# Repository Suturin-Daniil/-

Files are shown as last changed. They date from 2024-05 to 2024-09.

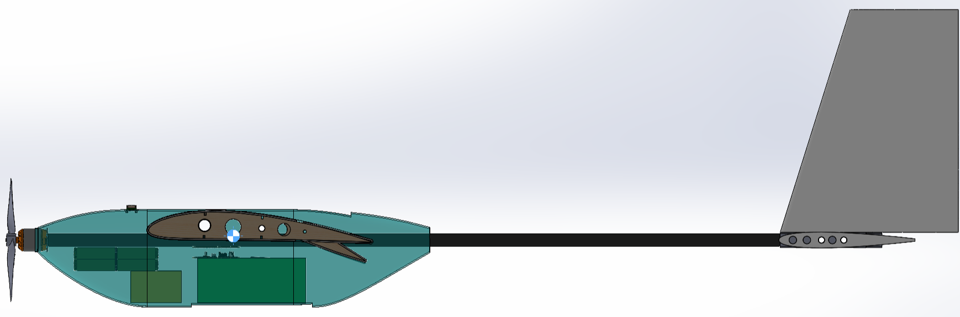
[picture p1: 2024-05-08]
PreliminaryDesign/Images/SideViewTransparentWithCG.png

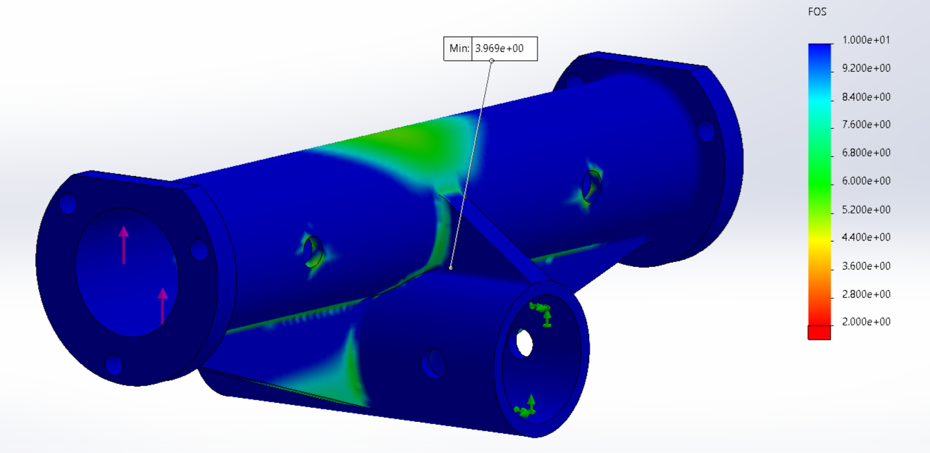
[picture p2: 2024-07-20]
Manufacturing/Отчет/ConnectorFOS.png

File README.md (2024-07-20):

# Репозиторий команды ФАКИшники СКАТ2024

В этом репозитории содержится процесс разработки ЛА командой "ФАКИшники" в рамках студенческого конкурса авиамодельного творчества СКАТ 2024.

## Структура репозитория

- **ConceptualDesign** - папка содержит резльтаты концептуального дизайна ЛА. Описание аэродинамической схемы. Начальная модель ЛА

- **PreliminaryDesign** - папка промежуточного отчета, содержащая детализированую модель ЛА, начальные аэродинамические и прочностные исследования. Описано бортовое оборудование

- **Manufacturing** - папка производственного отчета, содержит конечный вариант детальной модели ЛА, представлены результаты численного моделирования полета ЛА, статической и динамической стабильности. Прочностные расчеты

- **FlightController** - содержит электрические схемы полетного контроллера и платы распределения питания собственной разработки, а также проекты EasyEDA. Приложены gerber файлы печатых плат

- **Costings** - смета на полетный контроллер и ЛА

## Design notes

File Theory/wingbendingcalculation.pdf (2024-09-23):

### Wing Bending Calculations

Lab 10 Lecture Notes

Nomenclature

L

y | spanwise coordinate
q | net beam loading
S shear
M bending moment
θ | deflection angle (= dw/dx)
w | deflection
κ | local beam curvature
′ | lift/span distribution

′

S

η | normalized spanwise coordinate (= 2y/b)
c | local wing chord
wing | wing area
b | wing span
λ | taper ratio
E Young’s modulus
δ tip deflection
N load factor
m wing mass/span distribution I bending inertia
i | spanwise station index
n | last station index at tip

L lift
W weight
g | gravitational acceleration
()o | quantity at wing root

Loading and Deflection Relations
The net wing beam load distribution along the span is given by
′ | ′ q(y) = L (y) − N g m (y) | (1)

where m ′ (y) is the local mass/span of the wing, and N is the load factor. In steady level flight we have N = 1. The net loading q(y) produces shear S(y) and bending moment M(y) in the beam structure. This resultant distribution produces a deflection angle θ(y), and deflection w(y) of the beam, as sketched in Figure 1.

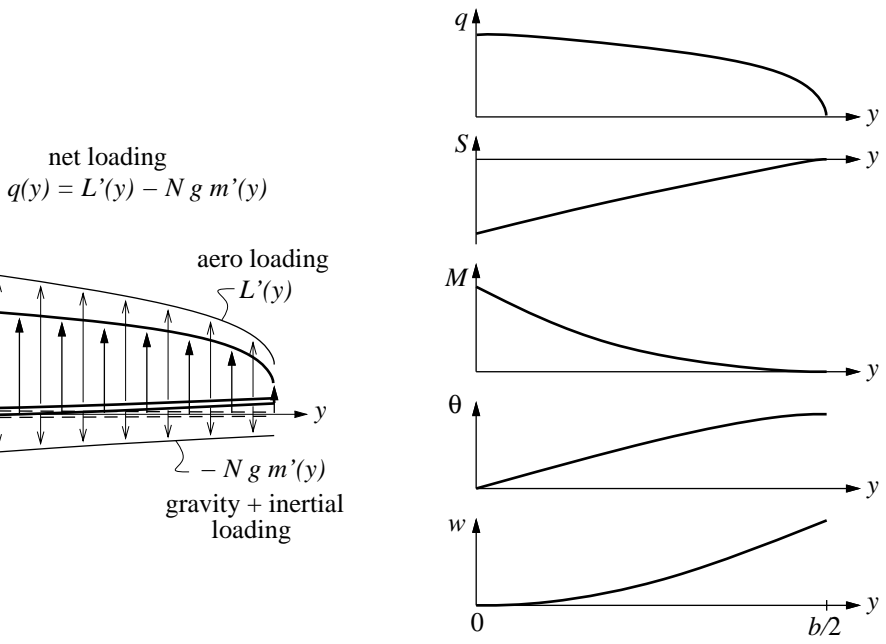
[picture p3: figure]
net loading q(y) = L’(y) − N g m’(y); aero loading; gravity + inertial; loading
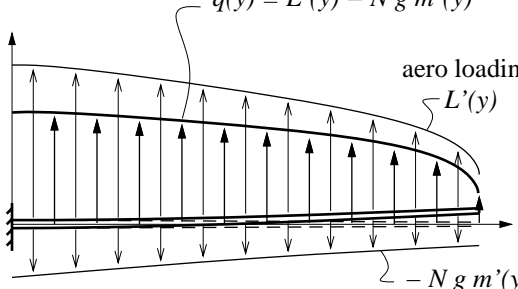
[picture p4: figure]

Figure 1: Aerodynamic and mass loadings, and resulting structural loads and deflection.

The standard differential equations derived via simple Bernoulli-Euler beam model, with the primary structural axis along the y direction, relate the loads and deflections to the loading q(y) and the bending stiffness EI(y).
dS | = q dy | (2)
dM = S dy | (3)
M dθ = | dy | (4) EI
dw = θ dy | (5)
To allow integration of these equations, it’s necessary to impose four boundary conditions. For a cantilevered wing beam, they are
y = b/2 : | S = 0 | (6)
y = b/2 : | M = 0 | (7)
y = 0 : | θ = 0 | (8)
y = 0 : | w = 0 | (9)

Load Distribution
The lift distribution L′ (y) needed to define q(y) depends on the induced angle αi(y) and hence the overall wing shape in a complicated manner. One reasonable simplification is to assume that the net aerodynamic + weight loading in equation (1) is proportional to the local chord,

y

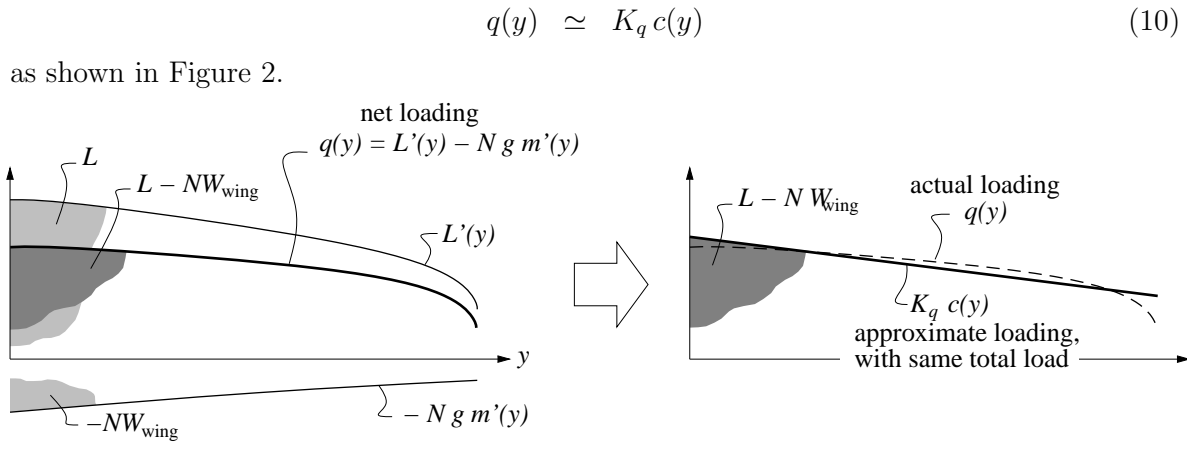
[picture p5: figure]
as shown in Figure 2.; net loading; wing; L − N Wwing; approximate loading, with same total load; actual loading

Figure 2: Net loading assumed to scale as local chord c(y).

This is equivalent to assuming a constant local cℓ = CL, and that the local wing mass distribution m ′ (y) scales as the chord. The constant Kq is best set such that the approximate and actual loadings have the same total integrated loads.

b/2 | b/2

−b/2

Kq c dy = | −b/2
| (L ′ − Ngm ′ ) dy | (11)
Kq Swing | = L − NWwing | (12)
Kq | = L − NWwing
| Swing

= NWfuse

Swing

| | (13)

where Wfuse is the weight of the fuselage, defined as everything not including the wing.

Numerical Integration
Equations (2) – (5) can be numerically integrated for any given nonuniform q(y) and EI(y) distributions. All spanwise variables are defined at a suitable number of discrete spanwise locations y0, y1 . . . yi . . . yn−1, yn. The differential equations (2) – (5) above can then be approximated over the yi . . . yi+1 interval via averages and finite differences.
qi+1 + qi Si+1 − Si | = | (yi+1 − yi) | (14) 2
Si+1 + Si Mi+1 − Mi | = | (yi+1 − yi) | (15) 2
1 Mi+1 | Mi θi+1 − θi | = | + | (yi+1 − yi) | (16) 2 EIi+1 | EIi

θi+1 + θi
wi+1 − wi | = | (yi+1 − yi) | (17) 2

As indicated in Figure 3, this is equivalent to approximate integration via the Trapezoidal

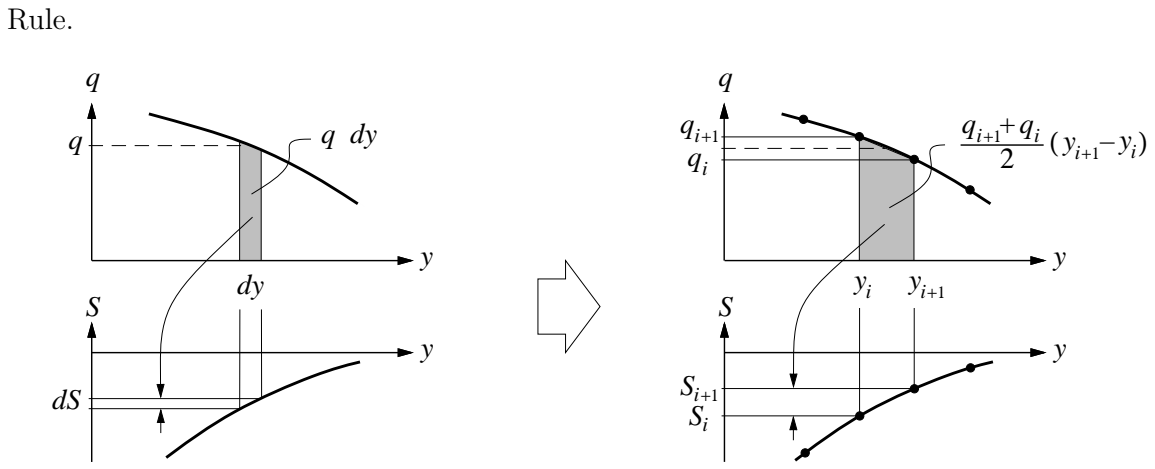
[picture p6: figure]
Rule.

Figure 3: Approximation of continuous differential equation with discrete finite differences and averages (Trapezoidal Rule).

For this statically-determinate problem, the beam equations can be discretely integrated (i.e. summed) in the order written above. The summation of each equation starts at the end where its boundary condition is applied. Equations (14) and (15) have their boundary conditions are at the tip at i = n, so they are summed from the tip inward after a simple rearrangement.
Sn | = 0 | (18)

q

Mn | = 0 | (19)
i+1 + qi Si | = Si+1 − | (yi+1 − yi) | (i = n−1, n−2 . . . 0) | (20) 2
Si+1 + Si Mi | = Mi+1 − | (yi+1 − yi) | (i = n−1, n−2 . . . 0) | (21) 2

For the two remaining equations (16) and (17), the boundary conditions (8) and (9) are at the root, so the summation proceeds from the root to the tip. After rearranging (16) and (17), and substituting i → i−1, we have

θ0 | = 0 | (22)
w0 | = 0 | (23)
θi | = θi−1 +

1
2

Mi
EIi

+

Mi−1
EIi−1
(yi − yi−1) | (i = 1, 2 . . . n) | (24)
wi | = wi−1 +

θi + θi−1
2 | (yi − yi−1) | (i = 1, 2 . . . n) | (25)

The summations above are readily implemented in a spreadsheet, as shown in Figure 4.
y | EI | q | S | M | θ | w

0

1

i

i +1

i −1

input data

0 0

0 0

formula

(20) | (21) | (24) | (25)

−1
n

n

Figure 4: Spreadsheet computation of arbitrary cantilever beam deflection.

Simplified Deflection Calculations
For preliminary or optimization work, the spreadsheet calculation of each candidate wing is unwieldy. For estimation, a very simple approximation is to assume that the beam curvature
d²w | dθ | M(y) κ(y) ≡ | = | = dy² | dy | EI(y)

is constant, and taken from some representative location such as the wing root at y = 0.

M0
κ(y) ≃ κ0 | = | (26) EI0

y
θ(y) = | κ0 dy = κ0 y | (27)
0
y | 1
κ0 y ² w(y) = | θ dy = | (28)
| | | 0 | | | 2

For a straight-taper wing with taper ratio ct/cr = λ, the chord distribution is

Swing | | | 2 | | | 2y
c(y) = | 1 + (λ − 1) | (29) b 1 + λ | b

and the corresponding approximate loading is then given by (10), and by the Kq defini-tion (13).

NWfuse | 2
q(y) ≃ Kq c(y) = | 1 + (λ − 1)η | (30) b | 1 + λ
2y
η ≡ | (31) b

To simplify the subsequent integrations, the y coordinate has been replaced with the equivalent and more convenient normalized coordinate η, which runs η = 0 . . . 1 root to tip. The shear and bending moment are then calculated by integrating equations (2) and (3).

b/2
S(y) = | q(y) dy | (32)
y
1 b S(η) = | q(η) dη | (33) 2 η
NW | 1 | fuse | 2 b = | 1 + (λ − 1)η dη | (34) b | 1 + λ 2 η
= NWfuse | 2 b 1 − η + (λ − 1)1
(1 − η²
) | (35) b | 1 + λ 2 | 2

b/2
M(y) = | S(y) dy | (36)
y
1 b M(η) = | S(η) dη | (37) 2 η
b² 1 | 1 = NWfuse | 2
1 − η + (λ − 1) (1 − η²
) dη | (38) b | 1 + λ 4 η | 2

b²
1 | 1 | 1 = NWfuse | 2
1 − η − | 1 − η² + (λ − 1) | 1 − η − | 1 − η³ | (39) b | 1 + λ 4 | 2 | 2 | 3

The root moment is then

b 1 + 2λ M0 ≡ M(0) = NWfuse | (40) 12 1 + λ

which is subsequently combined with (26) and (28) to get the following estimate of the tip deflection.

2 1 | b | M0 b² | NWfuse b³ 1 + 2λ δ ≡ w(b/2) ≃ | κ0 | = | = | (41) 2 | 2 | EI0 8 | EI0 | 96 1 + λ

Figure 5 shows κ(y) for three taper ratios for a solid wing, for which the stiffness varies as EI(y) ∼ c(y)⁴ . It can be seen that the κ = κ0 assumption is poor for a rectangular wing, but reasonable for wings of moderate to strong taper of λ = 0.3 . . . 0.5. Figure 6 compares the approximate deflections defined by (28) with the exact deflections, for the three taper ratios. For the untapered λ = 1.0 wing, the approximation considerably overestimates the tip deflection, but the tapered cases are quite reasonable.

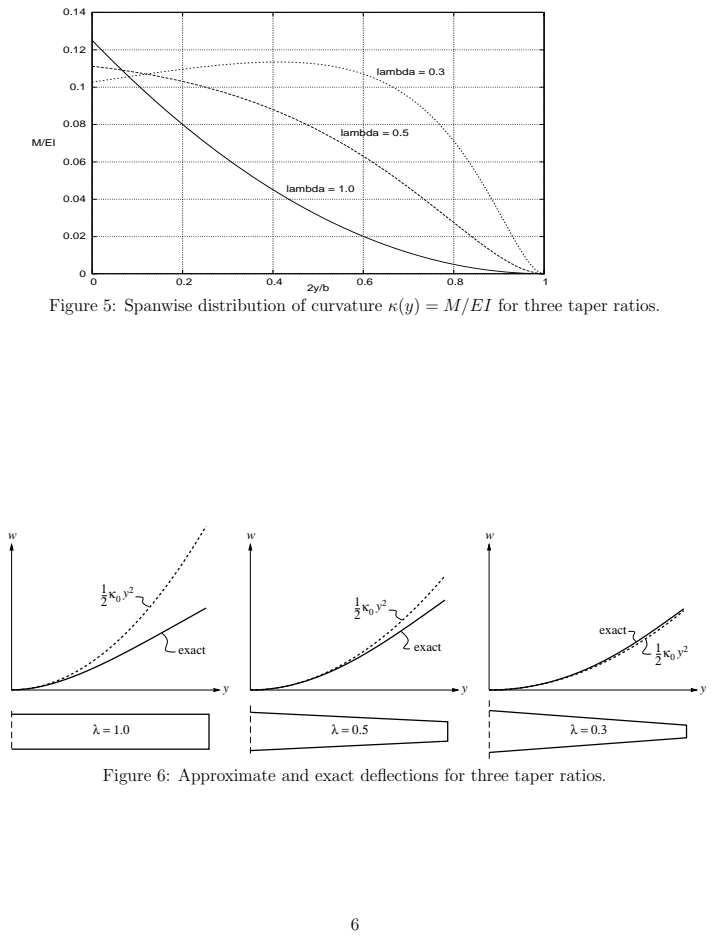
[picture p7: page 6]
lambda = 0.3; κ0 2 exact; y exact; exact

lambda = 0.5

lambda = 1.0

Figure 5: Spanwise distribution of curvature κ(y) = M/EI for three taper ratios.

Figure 6: Approximate and exact deflections for three taper ratios.

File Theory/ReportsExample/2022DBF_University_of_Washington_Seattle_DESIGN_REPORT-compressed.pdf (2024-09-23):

2021-2022 Design Report | University of Washington

## Contents

1 Executive Summary | 4
2 Management Summary | 5
3 Conceptual Design | 6
4 Preliminary Design | 16
5 Detailed Design | 27
6 Manufacturing Plan | 41
7 Test Plan | 48
8 Performance Results | 54
9 References | 60

Nomenclature
Abbreviations
- ac: Aerodynamic Center
- AIAA: American Institute of Aeronautics and Astronautics
- APC: Advanced Precision
Composites
- APD: Advanced Power
Drives
- AVL: Athena Vortex Lattice
- BEC: Battery Elimination Circuit
- CAD: Computer Aided Design
- CG: Center of Gravity
- CNC: Computer Numerical
Control
- ESC: Electronic Speed
Controller
- FEA: Finite Element Analysis
- GA: Genetic Algorithm
- GM: Ground Mission
- IMU: Inerital Measurment Unit
- LiPo: Lithium-Polymer
Battery
- M#: Mission Number
- MTOW: Max Takeoff Weight
- NACA: National Advisory
Committee for Aeronautics
- NiCd: Nickel Cadmium
Battery
- np: Neutral Point
- OpenVSP: Open Source
Vehicle Sketch Pad
- PLA: Polylactic Acid
- PC: Polycarbonate
- PET(G): Polyethylene
Terephthalate (Glycol)
- PKG: Package
- PWM: Pulse-Width
Modulation
- RX: Receiver
- STOL: Short-Takeoff and
Landing
- TO: Topology Optimization
- UW: University of Washington
- VLM: Vortex Lattice Method
- XPS: Extruded Polystyrene

Symbols

- AR: Aspect Ratio
- Ci

: Coefficient of Generic
Quantity
- D: Drag Force
- e: Oswald’s Efficiency
- f: Skin Friction
- F F: Form Factor
- F OS: Factor of Safety
- g: Gravitational Acceleration
- i: Incidence Angle
- L Lift Force
- m: mass
- N: Syringes per Flight Time
- n: Load Factor
- Q: Interference Factor
- S: Area
- s: Distance
- T: Thrust
- v: Velocity
- W: Weight
- z: Vertical Distance
- α: Angle of Attack (AOA)
- δ: Control Surface Deflection
- ζ: Damping Ratio
- µr Rolling Friction Coefficient
- ψ Yaw Angle
- τ : Period
- ω: Angular Frequency

Non-Symbol Subscripts

- a: Aileron
- e: Elevator
- f: Flap
- l: Roll Moment
- m: Pitching Moment
- n: Yaw Moment
- TO: Takeoff

## 1 Executive Summary

This report details the design, manufacturing, and testing of an Unmanned Aerial Vehicle to compete in the

American Institute for Aeronautics and Astronautics (AIAA) Design Build Fly (DBF) competition. The objective

of the competition is to construct an aircraft capable of carrying a payload of syringes and repeatedly deploying

vaccine packages on the ground without setting off 25G shock sensors. The competition mandates that the

aircraft stays within 8 ft linear dimensions, that the aircraft does not carry more than 100 Watt-hours of energy,

and that the aircraft is not of vertical takeoff or lighter than air configuration. Furthermore, the aircraft must follow

codes specified in the Federal Aviation Administration (FAA) part 107 standards and must takeoff within 25 ft for

all flight missions.

The Huskyworks team optimized the aircraft, titled the UW-22 Albatross, to complete three flight missions and

one ground mission. During the ground mission, the team must load and unload Mission 2 and Mission 3 pay-

loads as quickly as possible. The first flight mission demonstrates proof of flight and takeoff within 25 ft. The

aircraft must complete three laps unloaded within the span of five minutes. For the second flight, the aircraft

is required to carry the Mission 2 payload (syringes) and fly as fast as possible. The third flight requires the

aircraft to take off and fly one complete lap, at the end of which the aircraft must land, remotely deploy a vaccine

package, and takeoff again. The cycle is repeated until all packages have been delivered or a mission duration

of 10 minutes is reached.

Score analysis was performed to help determine the aircraft configuration and payload. It was determined that

the number of syringes had the most impact on score, as the number of syringes carried in Mission 2 determined

the number of boxes that could be carried in Mission 3. The Albatross was designed to carry 60 syringes, with

a theoretical max limit of 78 syringes, for Mission 2 and deploy 6 packages for Mission 3.

Figure 1: UW-22 Albatross

The UW-22 Albatross is designed to maximize competition score

through reliability and balance across all missions. The aircraft is

72 in long, has a 96 in wingspan, and weighs 12.5 lb unloaded.

It is a dual-boom, high wing configuration with wing taper begin-

ning at the motor mounts. The aircraft will fly Mission 2 with a

total weight of 15.3 lb at 82 ft/s in 75 seconds. The aircraft will fly

with max takeoff weight for Mission 3 at 15.8 lb, deploying 6 vac-

cine packages over the course of 7 laps lasting approximately 46

seconds each. The aircraft has a hinged nose and empennage

for easy loading and unloading during the ground mission which

will be completed in 180 seconds.

## 2 Management Summary

HuskyWorks began this 2021-22 competition year with over 130 members, including 36% freshman, 20% sopho-

mores, 29% juniors, 12% seniors, and 3% graduate students. While these students study a variety of disciplines,

all team members share a passion for aircraft design. HuskyWorks is led by 10 elected officers who each man-

age a unique facet of club operations. The team is sponsored by over 22 companies, including MagniX, Eviation

Air, Electroimpact, Marymoor R/C Club, and The Boeing Company. These organizations collectively provide

substantial monetary and material sponsorship, as well as technical expertise and mentorship through regular

Design Review Board meetings.

### 2.1 Team Organization

The HuskyWorks team has a leadership hierarchy that best facilitates communication and organization. The

organization is managed by the Chief Engineer and the Project Manager, and is advised by two faculty advisors

who review designs and approve testing activities. The Chief Engineer is responsible for design integration

and establishing design constraints. The Project Manager schedules all project timelines and deadlines and

manages cross-team communication. The Business Lead is responsible for budgeting, fundraising, marketing,

and procurement. Each technical sub-team is run by a sub-team lead, who is responsible for analyzing and

defining requirements with the Chief Engineer, ensuring design requirements are met, and adhering to project

timelines.

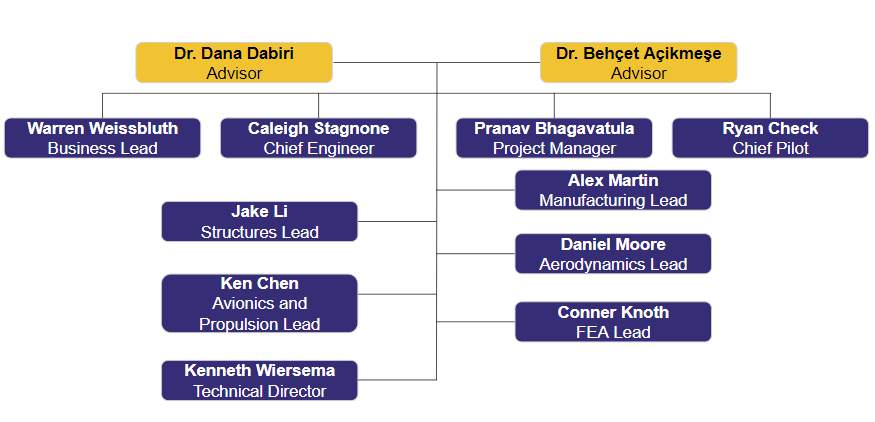
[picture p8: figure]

Figure 2: Team Organization

### 2.2 Milestone Chart

Huskyworks uses a variety of Gantt charts for timeline management. High level charts describe design mile-

stones, administrative deadlines, and provides an overview of the sub-tasks across the project life cycle. Meanwhile, low-level charts focuses on individual sub-task milestones and component deadlines. Fig. 3 is an example

of a high-level Gantt chart.

Figure 3: Milestone Gantt Chart

## 3 Conceptual Design

The 2022 AIAA DBF competition requires teams to design an aircraft to carry 30 mL syringes. Additionally, the

aircraft must be capable of storing 2.5 in x 3.0 in x 3.5 in (± 0.13 in) vaccine packages and deploying them such

that the attached 25G shock sensors are not set off. This section details the HuskyWorks team’s conceptual

design process, resulting in the selection of the aircraft configuration.

### 3.1 Mission Requirements and Constraints

### 3.1.1 Competition Scoring Summary

The competition score will be computed using both the Written Report Score and the Total Mission Score as

given by Eq. 1.

Score = W rittenReportScore · T otalM issionScore | (1)

Where the Written Report Score is calculated on a 100 point scale based on the quality of the written report. The

Total Mission Score is the sum of points from Mission 1 (M1), Mission 2 (M2), Mission 3 (M3), and the Ground

Mission (GM) given by Eq. 2.

T otalM issionScore = M1 + M2 + M3 + GM | (2)

Fig. 4 shows the competition lap layout. During each mission, the aircraft must takeoff within a 25 ft runway;

time begins for each flight when the throttle is advanced.

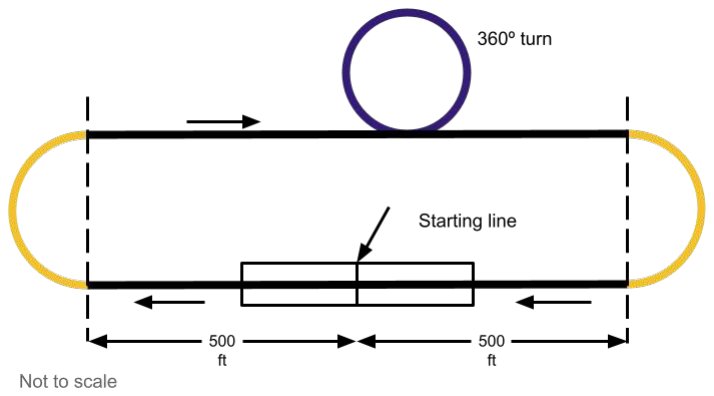
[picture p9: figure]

Figure 4: Competition Lap Layout

### 3.1.2 Mission 1: Staging Flight

Mission 1 teams must complete 3 full laps unloaded within a 5 minute window and with a successful landing.

Time ends when the aircraft passes over the finish line in the air. Successful teams will receive a score of 1.0

and unsuccessful teams will receive a score of 0. Eq. 3 shows the M1 scoring.

M1 = 1.0(successful) | (3)

### 3.1.3 Mission 2: Payload Flight

Mission 2 requires teams to fly three laps as fast as possible within a five minute window while carrying a payload

of syringes. Time ends when the third lap is completed in the air. The minimum number of syringes carried is

10. This mission is scored based on the time it takes to complete the mission and the number of syringes stored.

Each team’s score is normalized based on the maximum number of syringes divided by the best time scored

by a team at competition. The Mission 2 score is given by Eq. 4, where N is the number of syringes divided by

flight time.

M2 = 1 +

Nsyringes,UW

NSyringes,max

(4)

### 3.1.4 Mission 3: Delivery Flight

Mission 3 requires teams to deliver as many vaccine vial packages as possible within a 10 minute window. The

aircraft must fly a standard profile lap until completing the final downwind turn, at which point the aircraft must

land on the runway and taxi to the vaccine drop-off site, and remotely deploy one vaccine package. After the

package has been deployed, the aircraft must taxi to the start/finish line, come to a complete stop, and takeoff

again. This cycle is repeated until all packages have been delivered. Each vaccine package must be retrieved

by a Ground Crew Member and returned to the scoring table for evaluation of the shock sensors. If any sensor

has been set off, the package will not count. The maximum number of vaccine packages a team may attempt

to deliver is the lesser of either the maximum declared during Technical Inspection or the maximum number of

syringes flown in a successful Mission 2 divided by 10 rounded down to the nearest whole number. The scoring

for this mission is determined by the number of undamaged vaccine packages delivered normalized to the max-

imum number of packages delivered by a team at competition. Eq. 5 can be used to calculate Mission 3 score.

M3 = 2 +

Ndeployments,UW

Ndeployments,max

(5)

### 3.1.5 Ground Mission: Operational Demonstration

Teams must demonstrate the aircraft’s ability to complete Missions 2 and 3 on the ground prior to flight. This

mission is timed, beginning when the Ground Mission Official says “GO”. At this time, the Assembly Crew Member

must load the full Mission 2 payload into the aircraft, after which the Assembly Crew Member must run back to

the start/finish line to stop the timer. The timer will be reset, and the assembly crew member must again run to

the aircraft when the ground mission official says “GO” and unload the Mission 2 payload. The Crew Member will

then replace it with the Mission 3 payload, the timer stopping again when the assembly Crew Member crosses

the start/finish line. The Mission 3 payloads must be remotely deployed one at a time and returned to the official

to validate system functionality. Failure to deploy the maximum number of vaccine vial packages declared at

Technical Inspection will result in an incomplete mission. Scoring for this mission is shown in Eq. 6

GM =

tmin

tUW

(6)

### 3.2 Sensitivity Analysis

The sensitivity analysis of the competition aircraft was generated by the Scoring Optimization Algorithm devel-

oped by the HuskyWorks team. This provided the team with an multiple outputs; the optimal output was then

selected based on viability. The outputs were used as a baseline to generate a parameter sensitivity plot. The

following section discusses this two-step process.

### 3.2.1 Score Analysis

The scoring analysis was approached from a statistical perspective, distinguished from the traditional determinis-

tic point of view, such as solely relying on equation derivations. Specifically, the team developed a mathematical

flight model and used a Genetic Algorithm (GA) to optimize it to determine the best configurations under various

circumstances. To conclude the analysis, all parameters of each configuration were altered to test their sensi-

tivity to the overall score.

The mathematical flight model was the baseline of the numerical analysis. Following the success of the score

optimization project from the previous year, this model was dervied with adaptations for 2021-2022 rules. The

essence of the model is power balance during the flight, combined with the empirical formulae of peripheral de-

vices obtained from previous years, such as the thrust produced by motors. This model was then outfitted with

equations identified in the mission scoring breakdown to create a performance evaluation score. The Ground

Mission and Mission 1 parameters were omitted during this analysis because they contribute little to the syn-

optic scale evaluations. Eq. 7-9 are some representative equations that relate the mathematical model to the

competition, with all constants in their SI base unit.

Lcourse =

4 · π ·

v

2

amax,M2

+ 609.6, M2

4 · π ·

v

2

amax,M3

+ 609.6, M3

(7)

M2 =

Nsyringe

tm2

, tm2 ≤ 300

0, otherwise

(8)

M3 = Nlap = min {

600
Lcourse/vM3+tdeploy

,

Nsyringe
10

(9)

Unique to the competition in 2021-2022 is the limit of the course length by maximum acceleration during bank-

ing. Additionally, the Mission 2 score equation is limited to a time within 300 seconds and the Mission 3 score

is constrained either by the syringe payload from Mission 2 or the number of laps. Note that all mission scores

are non-dimensional.

After building the mathematical model, the team fed it into the GA to seek out the optimal configurations. GA is a

search process inspired by Charles Darwin’s theory of natural selection, in which the fittest individual is selected to reproduce the next generation. Gaussian noise was added to each parameter during the reproduction to

mimic the genetic mutation. Next, the mathematical model calculated the entire generation’s evaluation score

and selected the best. Some random samples (usually not the best ones) from the current generation were

selected to pass to the next generation to help the entire generation get out of local maxima. The process was

repeated until convergence. GA is also an iterative process, in which the team has to change the hyperparame-

ters and constraints to compare different outputs. Since the mathematical model’s convexity is not guaranteed,

i.e., multiple local minima existed in the domain, the team started with overestimated constraints, where no indi-

vidual survived. Then, the harsh restrictions were gradually relaxed until there were acceptable configurations.

The team executed each iteration several times to reduce the randomness of the algorithm. The team chose

the hyperparameters of simulating 50 generations with a size of 10,000 in which only 500 configurations survived.

Testing the sensitivity of the parameters was also a statistical process. The team introduced a multiplier to all

parameters and recorded the score changes for every 500 configurations that survived. The average score

changes were plotted in order to serve as general guidance in the latter configuration selection, shown in Fig.

5. Using the values generated by the model, the wing area, lift coefficient, empty weight, and velocity were

calculated.

Figure 5: Score Sensitivity of Mission Parameters

### 3.2.2 Performance Analysis

After accounting for the needed modifications to the GA, the team took the remaining parameters and set them as

target values during the preliminary design and configuration selection of the aircraft. The parameters selected

drove each design decision during preliminary and detailed design, guiding the design methodology approach.

Table 1: GA Optimized Parameters

The GA output a set of suggested performance parameters shown in Table 1. The sensitivity analysis determined

that the number of syringes carried in Mission 2 had the greatest impact on competition score, as the number

of boxes a team is allowed to deploy in Mission 3 is capped by the number of syringes stored in Mission 2. The

maximum score configuration determined by the algorithm is listed in the first row of Table 1, indicating that the

optimal aircraft could carry 70 syringes and deploy 7 packages. All configurations were assumed to complete

the deployment cycle within 45 seconds.

### 3.3 Subsystem Design Requirements

The design requirements were developed from the scoring equations and competition guidelines in order to

guide the design process. The initial configuration and design approach were guided by an analysis of the

scoring equations, selecting configurations to maximize competition score. Competition requirements state the

linear dimensions of the aircraft must not exceed 8 ft. Additionally, the aircraft must not be of lighter-than-air

configuration or have rotary wings. Propulsion batteries must be NiCad or LiPo, and the propulsion power

stored energy cannot exceed 100 Watt-hours. The aircraft must be capable of takeoff within 25 ft and may not

switch configurations between missions.

### 3.3.1 Lifting Surfaces

With a 25 ft takeoff distance, aerodynamic design focused on ensuring the aircraft had enough lift to get off the

ground within this distance at all payload and power configurations. It was noted that the critical flights were

the first and last flights of Mission 3: the first requires short takeoff with maximum payload and the last requires

takeoff with minimum battery power. Optimization studies indicated the need to maximize wing span to increase

wing area.

### 3.3.2 Propulsion System

From the scoring analysis, the endurance target was set at 6 deliveries in M3. After initial calculations, it was

determined that the system be designed around the maximum energy limit of 100 Watt-hours, as the increase in

propulsion performance significantly outweighs the increase in weight of the system. According to calculations,

a 900 Watt average power allowance was determined for M3, besides a 3000 Watt maximum allowance for M2.

### 3.3.3 Payload

The fuselage was designed surrounding the Missions 2 and 3. Scoring analysis concluded that maximizing the

number of syringes stored in Mission 2 greatly impacted the score; thus, the fuselage was designed to maximize

the storage capacity. The required length of the Mission 3 mechanism to fit 6 packages and their tolerances

determined the length of the fuselage. The mechanism was designed to fit the desired number of boxes at their

maximum possible length (3.5 + 0.13 in). The team also paid special attention to the reliability of this mechanism,

as it was determined that the ability to successfully complete all deployments during mission 3 depended on the

mechanism’s ability to repeatedly make package drops without variance in drop time or mechanism parts failing.

### 3.4 Configuration Selection

The following section details the design considerations the team completed throughout the conceptual design

phase demonstrated via weighted decision matrices. Each figure of merit was assigned a weight between 0 and

1 based on the impact each had on the score. A score between 0 and 10 was assigned to each configuration

for each figure of merit, yielding a total score out of 10. The highest score out of 10 was determined to be the

optimal configuration. The score for each component was determined through research during trade studies.

### 3.4.1 Aerodynamic Configuration Selection

For the general aerodynamic configuration of the aircraft, three different configuration ideas were presented:

A conventional single wing with horizontal stabilizer, a tandem wing design with two wings, and a tri-surface

which had a wing, horizontal stabilizer, and canards located towards the front of the plane. L/D and CD,0 for

representative models were evaluated in OpenVSP. As summarised in Table 2, the conventional configuration

was chosen on the basis of it being a familiar design that was well documented for aerodynamic and control

parameters, in addition to having the highest lift. While it had the smallest wing span, that characteristic was

judged to be the least important when compared to the complexity of the other two designs. Additionally, the

conventional configuration was chosen on the basis that the horizontal stabilizer needed to be located further

back on the plane. With the weight restrictions, the conventional design would require the least structural support.

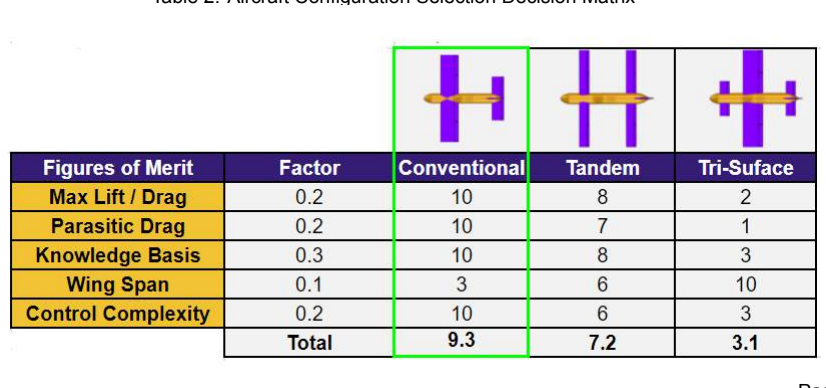
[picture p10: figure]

Table 2: Aircraft Configuration Selection Decision Matrix

### 3.4.2 Wing Position

For the position of the wing, three different configurations were found, with a low, mid, or high wing, as shown

in Table 3. The high wing was deemed to be the most suitable configuration due to it having the highest Lift

to Drag ratio and stability, and additionally removing complications with deployment through the bottom of the

fuselage that the other two designs would require, and giving the maximum amount of propulsion flexibility by

being higher off the ground, allowing for a greater variety of propellers to be used.

Table 3: Wing Position Decision Matrix

### 3.4.3 Wing Shape

For the shape of the wing, four different configurations were discussed: straight, tapered, elliptical, and swept.

As summarized in Table 4, the tapered wing was chosen due to lower induced drag relative to the straight wing,

without adding additional manufacturing complexity. The tapered and swept wings out-scored the elliptical due

to manufacturability. The loss of lift with reduced planform for a decrease in drag was acceptable as due to the

battery requirements, the aircraft needed to have the lowest possible drag.

Table 4: Wing Shape Decision Matrix

### 3.4.4 Tail Geometry

Stability, versatility, and manufacturability were high priorities when evaluating tail design. Stability of the plane

in flight was emphasized, as it was the primary role of the tail. Versatility was the measure of how well the

design accommodated the package deployment mechanism. Manufacturability took into account the difficulty of

assembling the tail according to the design. Low drag and low weight were prioritized, but less so, due to the tail’s

relative size to the rest of the plane. Strength was of little concern, due to the low aerodynamic forces relative to

the high strength of materials to be used in the tail. Redundancy examined the level of control the plane would

have if a control surface was damaged or inoperable, but was not significant enough to warrant a higher factor.

Summarized in Table 5, the team initially selected the High Boom configuration due to it’s high score in versatility

and the structural benefits to the dual-boom design. After initial flight testing, the horizontal stabilizer was moved

to the base of the vertical stabilizer to improve increase the pitching moment from propwash, so the aircraft could

takeoff well within 25 ft.

Table 5: Decision Matrix for Tail Geometry

### 3.4.5 Propulsion Configuration Selection

The first step was to determine the number of motors to be used (each driving one prop). Following limits set

in Section 3.3.3 and other demands, performance metrics were ranked as follows: takeoff thrust, practicality,

system lightness, ground clearance, and high speed thrust. Takeoff thrust was of highest priority to ensure

the airplane always takes off within 25 ft. Practicality was second, since complications in certain propulsion

designs may severely compromise the airframe. Tied for second was system lightness, to aid weight-reduction

and overall performance. Ground clearance aids M3 deployment by allowing the airframe to be lower to the

ground and help M3 deployment, but was ranked lower due to its lesser impact on improving score. Lastly, any

high speed performance that does not compromise completion time of M2 and the number of M3 deliveries was

deemed sufficient since a low speed, high energy-efficiency concept was adopted for the airplane. Based on the

decision matrix shown in Table 6, the twin-motor configuration was selected. Mounting the motors to each side

of the wing in a puller configuration was adopted since it was the most structurally efficient. Additionally, counter-

rotating props were adopted, to balance moments and generate outwash, improving stall characteristics.

Table 6: Propulsion Decision Matrix with Propellers Listed Below Motors.

The weight of the mechanism and speed at which the mechanism could drop packages were the two principle

considerations in payload deployment design. The speed at which the deployment mechanism could deploy a

package was a principal concern because only ten minutes are allowed to complete all laps and package deploy-

ments. Other key factors considered were size, complexity, adaptability to package size tolerances, and ease of

manufacturing. Size of the mechanism was considered in terms of both height and length, as these dimensions

directly impacted fuselage and aerodynamic design. Complexity was another factor considered, as the more

complex the design became, the more points of failure it had, in turn reducing its reliability. Table 7 shows three

conceptual designs: the rack and pinion, the conveyor belt, and a mechanism that moved packages in discrete

increments. The rack and pinion design scored highly for weight, size, speed, and tolerance adaptability. It

was the most compact and appeared to save the most weight. Research and experimentation also suggested it

would be capable of dropping packages quickly. By making use of laser cutting and 3D printing, manufacturing

this design was relatively simple.

Table 7: Mission 3 Deployment Mechanism Decision Matrix

### 3.5 Final Conceptual Design Configuration

The UW-22 Albatross final configuration is dual-boom, high-wing, twin-motor aircraft with tricycle landing gear.

The wings were tapered beginning at the motor mounts to provide an optimal lift distribution across the wing and

reduce weight at the tips, where the wing experiences the least load. Maximum takeoff performance under any

payload is ensured by the twin motors. This aircraft is designed to carry 60 syringes for Mission 2 and deploy

6 vaccine packages for Mission 3. This yields a total payload weight of 2.5 lb and 3.5 lb for Missions 2 and 3,

respectively.

## 4 Preliminary Design

Once conceptual design and trade studies were completed, the HuskyWorks team transitioned into preliminary

design, where the aircraft configuration was analyzed and decisions regarding the shape, size, and manufactur-

ing of the aircraft were made. Fig. 6 details a high-level overview of the design process.

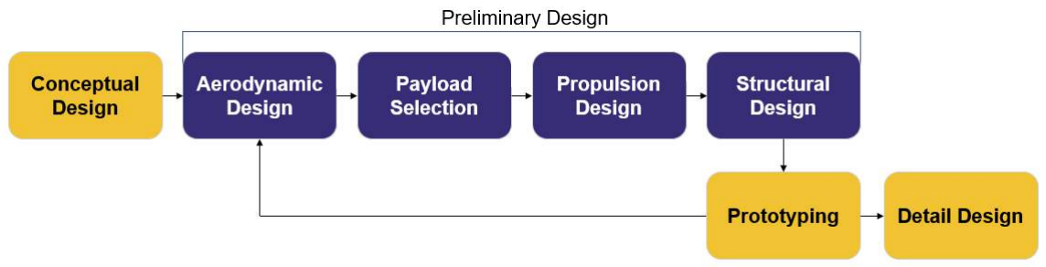
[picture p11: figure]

Figure 6: Design Flow Chart

### 4.1 Design Methodology

At the start of the competition cycle, the HuskyWorks team divided into sub-teams based on team member

interest and expertise. The team worked to design an aircraft that maximized payload storage for Mission 2 and

flew reliably for Mission 3. The preliminary design began after the desired payload storage capabilities were

determined. Through genetic optimization the team determined that it was ideal to deploy 6 vaccine packages

for Mission 3 and carry 60 syringes for Mission 2. Based on the payload requirement, the aerodynamics team

analyzed several airfoils based on stability, stall angle, lift, and drag that would produce the required lift to takeoff

within 25 ft for all flight missions. The structures team focused on weight optimization, identifying a need to move

away from a previously used composite monocoque fuselage structure towards a significantly lighter alternative

using plywood, balsa wood, and covering film. The propulsion team designed systems to maximize and balance

efficiency for both missions. The manufacturing team provided input on the manufacturability of a given design.

In order to ensure each design was completed thoroughly, the HuskyWorks team designed the Albatross with

input from members across all sub-teams.

### 4.2 Design Trade Studies

Listed in the following section are the trade studies conducted to select the configuration that was optimal for

this year’s competition. As 6 boxes and 60 syringes were to be stored in the Albatross, the trade studies were

performed with such a payload in mind.

### 4.2.1 Tail Sizing

To determine the preliminary size and positioning of the tail, typical tail volume coefficients for general aviation

were defined for the initial design; a horizontal tail coefficient of 0.6 and a vertical tail coefficient of 0.06. Using

estimates for expected wing reference area, wing mean aerodynamic chord, and location of the center of gravity,

definitions of the tail volume coefficients were solved for tail reference area, giving initial estimates for the size of

the horizontal and vertical stabilizers. Due to calculations done by the propulsion team based on 20 in diameter

propellers, the booms were designed to be spaced 2.25 ft apart on the aircraft. The horizontal stabilizer was

then sized to have a span of 2.25 ft, to line up with the tail booms and taking into account the fuselage diameter.

A wing-tail ac distance of 36 in was selected, balancing reduction in tail area and maintaining sufficient stabilizer

thickness for manufacturing ease

### 4.2.2 Control Surface Sizing

Initial control surface sizing and design were done for four primary control surfaces: elevators, rudders, ailerons,

and flaps. These were based off of initial wing and tail dimensions available at the time and empirical guidelines

(1). For the elevator, span was taken to be 95% of the horizontal stabilizer span and chord was taken to be 25%

of the stabilizer chord. For the rudder, span was taken to be 90% of the vertical stabilizer span and chord was

taken to be 32% of the stabilizer chord. The ailerons were initially placed spanning from 50% of the wingspan to

90% of the wingspan. Finally, the flaps were designed to reach a design goal for lift coefficient of 2.3 (assuming

an uncorrected 1.5 CL,max without flaps). The percentage sizes of these control surfaces were based off of

preliminary design guidelines obtained by the aerodynamics team.

### 4.2.3 Propulsion Sizing

As described in Section 3.4.3, propulsion optimization was completed for each configuration before the choice

of configuration was made. This section focuses on the development of the twin-motor, as it was the final se-

lection; however, the sizing process was the same for all configurations. Continuing from the decision to utilize

the full 100 Watt-hour energy limit, the motor and prop combinations were investigated according to the order of

weighted performance metric, while staying within the 900 Watt average power allowance for M3 and the 3000

Watt power limit for M2. Additionally, anticipating the demand of counter-rotating props to counter moments on a

twin-motor airplane, the propeller choices were limited to those with makes of both orientations. After comparing

more than 20 motor and propeller combinations in propulsion calculator tool eCalc, the T-Motor AT4130 300KV

brushless outrunner and the APC 20X13E propeller were deemed to be the most appropriate combination (2).

The 20X13E was the optimal choice, as any propeller of a smaller diameter suffered a deficit of at least 3.3 lb of

static thrust per motor, defeating any advantage elsewhere. Any propeller of a larger diameter does not contain a

counter-rotating option, which could lead to severe controllability issues due to the size and torque they produce.

The T-Motor was considered best as it was the lightest of all motors that can produce high performance on the

20X13E without overheating. Additionally, it has a slim-tall form factor, which is aerodynamically advantageous.

Meanwhile, LiPo was chosen as the propulsion battery formula due to its much higher energy density with respect

to other formulas allowed under the regulations. Following the motor and propeller combination, the voltage of

a 6S battery was required to extract full potential, and hence the 6S 4500 mAh battery was chosen, landing at

99.7 Watt-hours of energy. With a 1.2 factor of safety applied to eCalc’s estimate of 143.5 A combined current

at max power, 40C was selected as the minimum discharge rate to enable 180 A of current.

### 4.2.4 Wing Structure

When determining the optimal wing structure, the HuskyWorks team investigated using a skin-supported carbon

fiber wing, XPS foam, XPS foam with fiberglass, and plywood with covering film (monokote). Table 8 was used to

compare these options based on manufacturability, strength, weight, and rigidity. Weight was the biggest factor

given the requirement for a short takeoff. Next was rigidity, which was important due to the need for the wing to

survive a 2.5G wing-tip loading test during the Technical Inspection. Manufacturability was ranked next due to the

complexity of the wing taper making some options much more challenging. Strength was ranked last due to the

material properties indicating that each material could undergo the forces without breaking. After a combination

of testing and research, the team selected an XPS foam and fiberglass wing for the competition aircraft. While

initially selecting a pure foam wing and implementing this on the Aerodynamic Prototype, the wing was observed

to deflect far too much under a wing-tip loading test on the aircraft at it’s empty weight. Thus, the decision was

made to reinforce the wings with 0.75 oz fiberglass. While carbon fiber wings and plywood/covering film wings

had benefits in rigidity and weight respectively, the downsides of the carbon fiber’s weight and plywood/covering

film’s manufacturability and rigidity yielded a lower total score.

Table 8: Wing Structure Decision Matrix

### 4.2.5 Fuselage Structure

The HuskyWorks team investigated monocoque and semi-monocoque fuselage structures for the Albatross. The

two structures were compared based on weight, payload storage capacity (volume), manufacturability, compati-

bility with deployment mechanism, cost, strength, ability to take an impact, and manufacturing speed (time). The

two highest rankings were compatibility with the mission 3 mechanism and weight. Mission 3 was prioritized due

to the fact that the fuselage was designed around the mechanism. Weight was important because of the 25 ft

takeoff distance limit. Volume had the second largest factor, as the sensitivity analysis indicated that an ability

to carry more syringes would have the highest impact on competition score. Time, manufacturability, cost, and

impact resistance were notable factors, however, they had little impact on the decision. While the monocoque

structure increased payload storage capacity due to the lack of a need for internal structures and had better

reusability (measured by impact resistance), it was more difficult to integrate the deployment mechanism and

weighed almost twice as much as the semi-monocoque fuselage. While the semi-monocoque structure did have

less internal volume and less impact resistance, the benefits of ease of manufacturing, weight, cost, and time

led the team to decide on this structure. A decision matrix summarizing these results is shown in Table 9.

Table 9: Fuselage Structure Decision Matrix

### 4.3 Aerodynamics

### 4.3.1 Airfoil Selection

Fleshing out the three-dimensional wing design, multiple airfoils, listed in Table 10, were considered from the

Airfoil Tools database (3). The initial collection of airfoils were selected from those used in previous years and

from those with L/Dmax extending over a large α range. From the set, the minimization of CD at cruise conditions

and maximizing CL,max were prioritized. Drag minimization allows higher airspeed, to which performance is most

sensitive, and maximizing CL,max improves STOL performance, critical to all flight missions. Margins for error

with in-flight stall and stability and with manufacturing were further considered. Airfoil ratings for each figure of

merit were based on the performance scaling relative to the average value of the figure of merit for all the airfoils

(average corresponding to a score of 5).

Table 10: Airfoil Selection Decision Matrix

Figure 7: Comparison of NACA 4412 and 6412 L/D

Airfoil performance were taken from tabulated XFoil

data for Re = 500, 000, on par with the Reynolds Num-

bers from previous competition seasons. Using the

results from Table 10 the NACA 4412 and 6412 air-

foils were selected as possible airfoils. Based on re-

view of the L/D versus α curves, shown in Fig. 7, the

NACA 6412 was selected in the end due to its higher

and broader L/D peak. To minimize drag in M3, for

which flight endurance is most important, a wing incidence angle of 3.75◦ was selected, providing the M3

lift-coefficient of 0.83 at 0

- α. Finite wing corrections

are applied to the airfoil lift-curve slope (4). To simplify analysis symmetric airfoils were chosen for the horizontal

and vertical stabilizers of sufficient thickness for manufacturing ease (NACA 0012 and 0008, respectively).

### 4.3.2 Aircraft Drag Analysis

Lift and drag performance of the Albatross were evaluated using the Vortex-Lattice Panel codes available in Mark

Drela’s Athena Vortex Lattice (AVL) and the open-source Vehicle Sketch Pad software (OpenVSP) developed

by NASA. Both programs are based on linear models and lack viscous boundary-layer subroutines, limiting their

accuracy to small angles of attack. OpenVSP’s Parasite Drag Tool was used to estimate the parasitic drag due to

each airframe component. Per Eq. 10, this tool evaluates the equivalent skin-friction coefficient (Cf ), form-factor

(F F), interference factor (Q), and wetted area to calculate the scaled CD,0 of each component i (5).

CD,i =

Swet,i

Sref

QiCf,iF Fi | (10)

Using the maximum flight weight and predicted airspeed of the Albatross for each mission Eq. 11 was used

to estimate the cruise lift coefficient of each mission. These results are included in the predicted performance

summary (Table 15).

CL =

L

qSref

=

W qSref | (11)

(a) (b)

Figure 8: Vortex-Lattice Analysis Models: (a) AVL, (b) OpenVSP / VSPAero

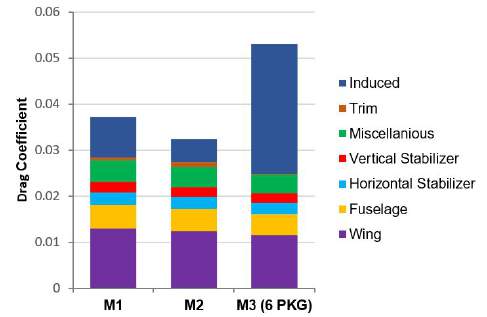
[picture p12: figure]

Figure 9: Breakdown of Mission Drag into Components

Control surface deflections and angle-of-attack were

trimmed in AVL to yield the required lift coefficient for

steady-level flight. This evaluation further calculated

the induced drag at cruise. Trim drag was evalu-

ated using the trimmed elevator deflections from AVL

and methods from (4), assuming the elevator acts as

a dual-direction horizontal-stabilizer flap. The drag-

build up for parasitic, induced, and trim drags for each

mission are shown in Fig. 9, yielding drag coefficients

of 0.037, 0.032, and 0.053 for M1, M2, and M3, re-

spectively.

(a) (b)

Figure 10: Aircraft Lift and Drag Performance

The drag polar and L/D curve for each VLM model are shown in Fig. 10. The parasitic drag calculated with

OpenVSP’s Parasite Drag module served as the CD,0 for the AVL simulation. Data from the half-body wind

tunnel test with 0.18 shift in CD is shown along the VLM results to highlight the sharp increase drag for viscous,

non-linear flows at high CL. Both experimental and numerical models predict a L/D peak within 2

- < α < 3

◦

### 4.3.3 Wingtip Design

Figure 11: Lift Curve Variation with Endplate

Following primary wing design, the effect of endplates on

the wing tips of the Albatross was investigated through wind

tunnel testing of a 50%-scale half-body. This testing is fur-

ther detailed in Sect. 7.3.1. The endplates tested, shown

in Fig. 12, were designed to fence upper and lower surface

flows along the entire chord (a), reduce trailing-edge tip vor-

tex generation (b), and fence upper surface flow and mini-

mize surface area (c). The test setup limited the accuracy

of measured drag forces. Fig. 11 indicates little to no im-

provement in the lift of the Albatross. This is likely due to the

reduced tip chord size relative to the mean-aerodynamic-

chord and thus reduced distance over which air may spill over the tip and contribute to a wing-tip vortex.

(a) | (b) | (c)

Figure 12: Wing Endplates Tested in Wind Tunnel of Type (a), (b), and (c)

### 4.3.4 Flap Lift and Drag Analysis

Figure 13: CL and CD Change for Individual and Combined Sets of Plain and Slotted Flap Deflection

To help reduce the takeoff distance of the Albatross, slotted

flaps were selected for the inner flaps between the mounting

lines of the motors. Raymer predicts a 44% increase in flap

effectiveness for slotted flaps relative to plain flaps (1). Plain

flaps were selected for the outer flaps on the tapered section

of the wing to reduce manufacturing complexity. Using the

empirical methods of (4), Fig. 13 predicts the variation in lift

and drag with the deflection of the flaps, as designed.

### 4.4 Aircraft Stability Analysis

### 4.4.1 Static Stability

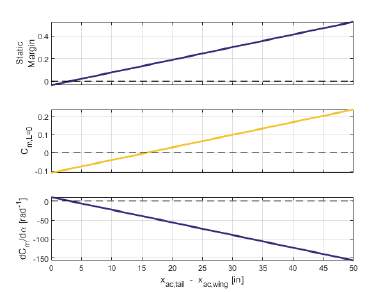
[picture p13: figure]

Figure 14: Figures for Horizontal Tail Placement for btail = 2.25 ft, ctail = 0.455 ft, and it = −4

◦

Implementing formulas from (6), a Matlab Script was used to gen-

erate figures equivalent to Fig. 14 for multiple horizontal stabilizer

incidences. A −4

◦
incidence was chosen, meeting longitudinal

static stability requirements and offering a margin for manufactur-

ing error and deviation in the assumed CG position. Accounting

for the full aircraft, AVL was used to calculated the principal sta-

bility and control derivatives for M2 listed in Table 11, which had

the most severe trim conditions. Each stability derivative sign is

correct to yield longitudinal, lateral, and directional static stability,

with a 0.225 static margin.

Table 11: M2 Stability and Control Derivatives Evaluated in AVL

### 4.4.2 Dynamic Stability

AVL was utilized to evaluate dynamic mode eigenvalues and damping frequency characteristics. Eigenvalues

for both trimmed cruise and trimmed takeoff conditions in Fig. 15 indicate that the Phugoid and Spiral modes

are unstable. The other dynamic modes each have negative real parts in their eigenvalues for all conditions.

In-line with this indicated stability, the damping coefficient, frequency, and period of oscillations in Tables 12-14

for the Short Period, Dutch Roll, and Roll modes, for all cases, meet the requirements for Level 2 (L2) handling

characteristic standards of (7). In this evaluation, the Albatross is assumed to mimic a Class II medium weight,

low-medium maneuverability aircraft.

For the unstable spiral mode, the mode doubling time falls within Level 3 (L3) requirements for all but M1 takeoff.

For the Phugoid mode however, the doubling time is significantly lower than the Level 3 requirement. With the

scale of the Albatross and increased response rate relative to that of full-scale aircraft, discussion with the pilot

determined that the predicted times-to-double are acceptable despite falling outside the guidelines of (7).

(a) (b)

Figure 15: Eigenvalues of Dynamic Stability Modes for Cruise (a) and Takeoff (b)

Table 12: Mission 1 Dynamic Mode Parameters (Cruise/Takeoff)

Table 13: Mission 2 Dynamic Mode Parameters (Cruise/Takeoff)

Table 14: Mission 3 Dynamic Mode Parameters at maximum payload (Cruise/Takeoff)

### 4.5 Predicted Aircraft Mission Performance

### 4.5.1 Power Curve

Figure 16: Available and Required Power vs. Airspeed

Using the parasitic drag estimates from OpenVSP, the ide-

alization of Eq. 12, and thrust versus velocity data from the

wind tunnel propeller testing detailed in Section 7.3.2, Fig.

16 was constructed (6). The figure indicates a maximum

airspeed of approximately 104.5 ft/s at maximum throttle

(corresponding to about 5,000 RPM for the motors).

D = qSref(CD,0 +

C

2
L
πeAR) | (12)

### 4.5.2 Takeoff

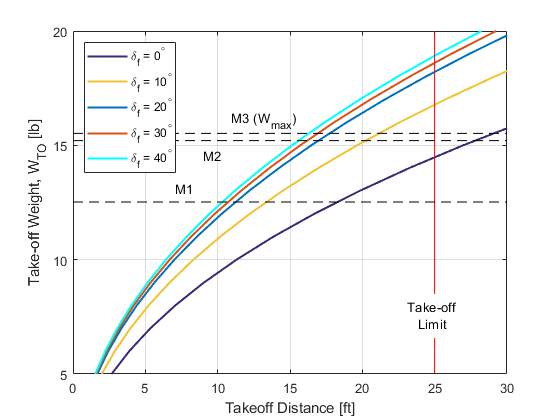
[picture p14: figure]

Figure 17: Variation in Takeoff Distance with Weight

An analysis of takeoff performance was performed to deter-

mine the required flap setting and verify the ability to take-

off within 25 ft for all flight conditions. Assuming the pres-

ence of ground effect and a rolling friction coefficient, µr of

0.05, the analysis utilized the wind-tunnel predicted thrust

and lift curves, used the average parasitic drag across the

missions, and required a 1.2vstall takeoff speed to ensure

a margin for performance error. Variance in lift and drag

coefficients with flap deflections were calculated using the

methods of (4). From Fig. 17, only for M1 is the aircraft

expected to be able to takeoff without flaps, but with an estimated 40◦ maximum deflection angle, sufficient flap deflection is available for M2 and M3 takeoff.

### 4.5.3 Turning Performance

Figure 18: Airframe Turning Rate Performance

Offering insight into the limits of turning performance, the in-

stantaneous turn rate was evaluated for the heaviest load-

ing condition of M3 in Fig. 18. The airframe’s corner speed is 71.8 ft/s, corresponding to 85.6deg
s

. For a given airspeed,

Fig. 18 may be used to calculate the instantaneous turn

radius according to Eq. 13.

r = v/ψ˙
(13)

### 4.5.4 Endurance

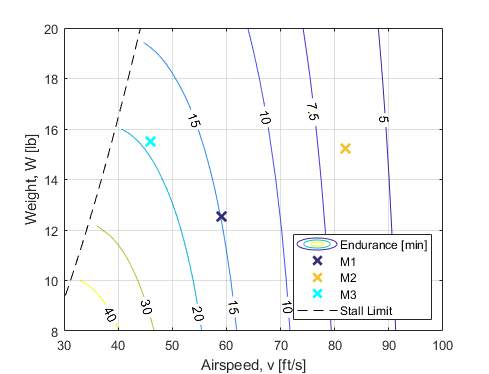
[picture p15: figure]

Figure 19: Endurance Variation with Airspeed and Weight

Fig. 19 shows that With the predicted mission airspeeds

of 59, 82, and 46 ft/s, the maximum endurance of the Alba-

tross at the maximum mission weights is 13.5, 5.9, and 19.8

minutes, respectively. The predicted mission flight times,

tabulated in Table 15 are well within these limits, offering

a reserve in battery energy for a non-ideal flight trajectory

or the need for a go-around. It may be noted that with the

maximum M3 weight with 6 PKGs used, the predicted M3

endurance is a lower bound.

### 4.5.5 Predicted Performance Summary

Predicted mission-specific flight conditions and performance are summarized in Table 15. The scoring param-

eters used in the table are the non-normalized flight scores: 1,

Syringe #

tM2

, and PKG number for M1, M2, and M3,

respectively. It was assumed that landing and taxi-to-deployment, deployment, and takeoff require 15, 20, and

5 seconds, respectively. The M2 and M3 score calculations and weight were based on a predicted 60-syringe

and 6 PKG payload, respectively.
Table 15: Predicted Performance of the Albatross

## 5 Detailed Design

The Detailed Design phase takes what was learned and selected during Trade Studies and Preliminary Design

to optimize the aircraft. As it has been seen in previous competitions that an aircraft that successfully completes

all three competition missions often places within the top 20 teams, the HuskyWorks team focused on aircraft

and mechanism reliability during this phase. Sub-system design was iterative to reduce weight and increase

efficiency and reliability. Additionally, detailed design carried over into manufacturing as many sub-systems

were iterated to optimize performance and improve manufacturability.

### 5.1 Dimensional Parameters

Table 16 shows the dimensions and electronic components of each aircraft system.

Table 16: Albatross Dimensions and Specifications

### 5.2 Structure Characteristics and Capabilities

The aircraft has a maximum takeoff weight of 15.57 lb with a load limit of 3.5G. Under such conditions, com-

ponents were designed to meet structural requirements of 1.5 FOS and mission expectations while minimizing

weight. The load experienced by the aircraft is broken down into three parts: aerodynamic loads, propulsive

loads, and ground loads. Aerodynamic and propulsive loads act on the wing-tail assembly, transferred through

tail booms, wing spars, skin, and mounts to fuselage longerons. Ground loads are dispersed by the main car-

bon fiber landing gear mounted on fuselage longerons and the nose gear on bulkheads, to create a tricycle

configuration.

### 5.3 Subsystem Design

### 5.3.1 Package Deployment System

The package deployment system consists of three main components: the frame, the carts, and the ramp. The

frame of the package deployment mechanism, pictured in Fig. 20, provides the shape of the mechanism and

holds the packages, while the carts, shown in Fig. 21, are responsible for moving the payload onto the ramp for deployment. The ramp lowers each package onto the runway without triggering the 25G shock sensors.

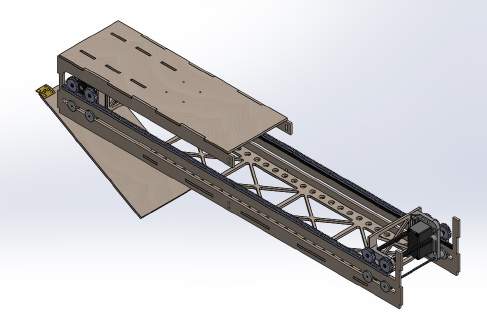
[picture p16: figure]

Figure 20: Payload Deployment System

The side panels of the frame have two slots, an upper

slot in which the gears run along the gear racks and

a lower slot in which alignment wheels run. Strength-

ening and alignment came from carbon strips glued

to the section of the frame on which the gears run

and the fuselage rib structure into which the frame

was integrated. Weight savings were achieved by in-

tegrating holes into various sections, namely the bot-

tom panel upon which vaccine packages rest. Addi-

tionally, spare space in the frame was minimized by

allowing the aircraft to house vaccine packages on the

ramp during its first lap of Mission 3.

Figure 21: Package Handling Cart

Two carts running along molded nylon gear racks provide the lin-

ear actuation required to move the vaccine packages along the

payload mechanism. A Parallax Feedback 360° servo was cho-

sen for it’s high stall torque, high RPM, and positional feedback

capabilities. It was determined that when pushing the full weight

of six vaccine packages, the Parallax 360° servo would be capa-

ble of running at approximately 100 RPM, allowing for the boxes

to be moved one box length per second. The gear ratio of the cart

actuation was chosen to maintain this desired cart travel speed,

while remaining within the servo’s torque restrictions. The gears

were selected to be 32 pitch as it was necessary for gears to be small enough to fit within the set size of the

frame, and large enough to avoid gear slippage due to inaccuracies in construction. Rollers were added to resist

the torque generated by the servo, hold the pinion gears against the rack, and keep the carts aligned in the frame.

A bottom mounted ramp was chosen to release packages due to simplicity of operation and effectiveness. The

desired angle of the ramp, and by extension, the ramp length, was determined by testing the optimal angle at

which the packages would slide down the ramp without triggering the sensors. The ramp was made to open

toward the rear of the aircraft for ease of package unloading. The hinge of the ramp was placed well in front of

the payload deployment opening to reduce the required opening size to fit a package, as well as reduce the total

length of the device. In order to fly with a package on the ramp, the ramp required a robust actuation device that

could hold the ramp shut with a package on it during flight. The actuation method was designed such that the control rod would be parallel to the servo arm in the closed position, minimizing the torque exerted on the servo

by the loaded ramp. As an additional precaution, a ramp servo with a sufficiently high stall torque was chosen

in order to resist the maximum possible torque when the control rod was perpendicular to the servo arm.

### 5.3.2 Package Deployment Automation

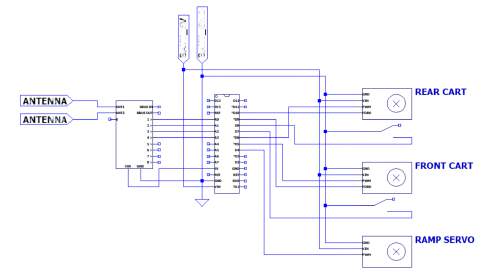
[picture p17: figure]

Figure 22: Mission 3 Mechanism Circuit Layout

An Arduino Nano was chosen to control the actua-

tion of the ramp and package handling carts. The

Arduino was given a dedicated FrSky RX8R receiver

and would be tasked with decoding commands from

a radio controller used by the ground crew. The Parallax Feedback 360◦ servos were powered with 7.2 V

from a dedicated BEC. The servo’s control wire was

connected to a digital pin on the Arduino Nano that

supplied a PWM signal. The servo provided the Ar-

duino with a positional feedback PWM signal as well.

Limit switches were placed on each end of the deployment mechanism such that the position of the package

handling carts could be zeroed. The cart’s exact distance from the switches could then be determined using

the servo’s positional feedback. This allows the packages to be moved such that the aircraft’s center of gravity

does not change between package deployments. The ramp servo is also actuated using a PWM signal from the

Arduino. The FrSky receiver uses four PWM signals to tell the Arduino when to begin the automatic deployment

cycle routine. The Arduino code also includes a manual override that allows the operator to directly control the

position of the ramp and carts.

### 5.3.3 Payload Storage Design

Figure 23: Syringe Storage Tray

The syringes for mission two are stored vertically on two syringe trays in front

of and behind the vaccine package deployment mechanism. These trays

are made up of a single panel of foam board with slightly undersized holes

such that syringes slide in with a tight fit. The panel can then slide into the

front and rear of the aircraft by hinging open the nose cone and empennage.

In order to maximize the number of syringes per unit volume, the syringes

are stored in alternating fashion such that the flanges of the syringes do

not interfere with each other. The vaccine packages are oriented inside the

deployment mechanism such that the longest dimension spans the width

of the fuselage while the intermediate dimension spans the length of the

aircraft. This orientation was chosen to decrease the fuselage length while

providing stability to the packages when sliding down the ramp.

### 5.3.4 Fuselage Design

The fuselage is a 7 in square cross section with 0.75 in fillets. The structure was composed of 8, 1/8 in plywood

ribs and 0.5 in unidirectional carbon fiber spars. Covering film was applied around the ribs for aerodynamics

and an access hatch was cut out of the film to access the batteries and flight controller stored above the mission

3 mechanism. 6 of the ribs served as the primary bulkheads, interfacing with other structural members includ-

ing the M3 mechanism, nose landing gear mount, and syringe storage mechanism. Two additional ribs were

included to help maintain the geometry of the fuselage when the covering film was applied. The two spars are

located 6 in apart and serve as the primary mounting points for the ribs, rear landing gear and wing.

Figure 24: Fuselage Structure with Mission 3 Mechanism

The first two bulkheads transfer the loads from the

nose landing gear mount onto the ribs and longerons,

as well as provide support for the deployment ramp.

The third and fifth bulkheads are the end plates for

the M3 deployment mechanism, and serve primarily

to maintain that structure. The fourth bulkhead is lo-

cated at the aircraft’s center of gravity below the first

wing spar. The additional two ribs were placed in be-

tween the third and fourth, and fourth and fifth bulk-

heads for geometric shaping. Stringers made of 1/32

in balsa wood curved to the shape of 0.75 in the fillet

were included on the fuselage corners to provide sup-

port for the covering film and maintain the shape of the fuselage cross section. The fillets were laid up with 0.75

oz fiberglass to stiffen the stringers. Additional stringers were added between the first and second, and fourth

and fifth bulkheads for alignment and additional covering film support.

### 5.3.5 Wing Design

The wing structure is composed of XPS foam cut into the shape of the airfoil, 0.75 oz fiberglass reinforcement,

plywood ribs, and 0.394 in unidirectional carbon fiber spars. As determined in preliminary design, the wing span

is 8 ft, divided into three sections separated at the motor mounts. The non-tapered center section spans 27 in

with a chord length of 14.4 in. The outer sections of the wing are tapered from a root chord of 14.4 in to a tip

chord of 5.05 in. Each side spans 33 in and their structure is identical.

The center wing section is attached to the fuselage via a 3D printed wing mount embedded in the foam that

interfaces with four aluminum mounts within the fuselage. The center wing section includes two wing ribs glued

onto the wing mount for transferring load from the foam to the spars and wing mount. The side panels of the

motor mount offer the load path from the foam to spars on the outer edge of the center wing. Two spars located at the quarter-chord and 2/3 of the chord extend out 15 and 5 in from the center section into the outer wings,

respectively. 0.75 oz fiberglass was laid up on the surface to provide torsional rigidity and bending stiffness.

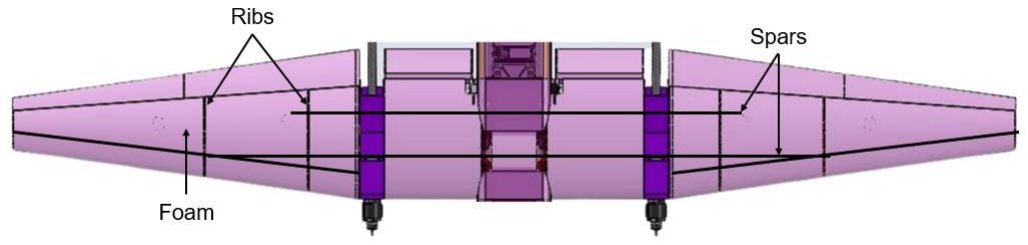
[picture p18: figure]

Figure 25: Wing Structure

The outer wing sections consist of one main spar following the taper of the wing along the quarter-chord. 4 ribs

were included to distribute the lifting load across the wing. Two ribs were included on either end to provide a load

path for the main spar; two ribs were included within the wing section to transfer the bending moment and shear loads to the center section. One layer of 0.75 oz fiberglass was laid up on the wing at a 45◦ angle to provide

torsional rigidity that could avoid tip stall and flutter due to the large wingspan.

Figure 26: Slotted Flap Mechanism

The wing has control surfaces along the entire wing span, with

slotted flaps adjacent to the fuselage, and separate flaps and

ailerons, each spanning 16.5 in as determined in preliminary de-

sign. The control surfaces were cut out of XPS foam and 1/32

in balsa wood was laid up on top to provide structural integrity

and torsional rigidity. The slotted flaps are attached via a hinges

attached to the motor mounts and on one of the wing ribs. The

hinges were offset below and in front of the hinge line to provide

a gap between the wing and the flaps and to achieve the slotted

flap result. FEA simulation was performed on wing structures.

The simulation indicated that at maximum stress, the structure had a factor of safety of approximately 2 com-

pared to material data. Additionally, a bending test was conducted on the wing tip sections to validate the FEA

results due to the complex loading conditions and structural layout.

### 5.3.6 Wing Mount

The design of the wing mounts was an iterative process. Throughout the design phase, mounts were designed in

CAD and reviewed, with an emphasis on weight reduction. Shown in Fig. 27, aluminum mounts were designed in

place 3D printed structure, resulting in a 87% reduction in weight while maintaining structural integrity. The wing

mount consists of 2 primary components, the 2 upper (PLA) in-wing sections, and 4 CNC machined aluminum

Figure 27: Aluminum Mount Iterations

longeron clamps. The wing spar runs through the embedded wing mount. 4 bolts are fastened from the top

through the wing into the 4 longeron clamps. This creates 4 contact points on which the wing loads disperse onto

the longerons. During the design process, FEA was used to verify that the wing mount could support the design

loads within a minimum factor of safety and to locate areas of

the design that were overbuilt or underbuilt. To simplify the FEA

setup, the forces due to the drag and aerodynamic moment on the

wing were ignored and the lift force was taken to act perpendicu-

lar to the longitudinal axis of the airplane. The lift force applied to

the wing mount in the FEA simulations was determined by mul-

tiplying the expected 15.57 lb MTOW by the maximum expected

load factor of 3.5G and by a 1.5 factor of safety, which yielded a

maximum expected lift load of 58.39 lb. This lift force was distributed equally across the four spar holes in the

wing mount.

### 5.3.7 Motor Mounts

The motor mount structure is designed to act as the transition point between the central wing and the wing tips.

Consisting of 2, 1/8 in plywood side panels and a double layered face plate, the assembly includes 2 sets of

3D-printed PLA clamps to secure the motor mount onto wing spars and secure the tail booms. This allowed for

both the tail and wing tips to be removed during transport. The 3D-printed tail boom clamp mounted onto the first

wing spar also holds servos for the rudders. The side panels act as additional ribs for the wings. Informed by

FEA, the motor mount design was iterated to remove unnecessary material and decrease drag. Shown in figure

28, the analysis determined that the plywood back plate was not needed and prone to failure. Additional material

was removed on the front plate to save weight and allow for cooling and ventilation of the motors. Covering film

was fixed across the top and bottom to reduce drag.

(a) Initial FEA | (b) FEA After Modifications

Figure 28: Comparative FEA of Motor Mounts

### 5.3.8 Landing Gear

The mount was designed to hold the nose gear in place under high impacts while allowing for the wheel to

be turned by a servo to steer the aircraft. Given that there are no longerons in the lower half of the fuselage,

the mount was designed to fasten between two ribs. Topology optimization was performed as the basis for the

design of this component due to the difficult loading conditions. The bounding box was defined as the entire

space between the front two ribs that would not interfere with the payload. A stress constraint was placed on

the model to ensure that it would not fail and a symmetry constraint was added to make the product easier

to manufacture. The objective of the optimization was to minimize the volume and the displacement under

maximum load with respective weights of 25% and 75%. The output mesh was smoothened and the part was

3D-printed for testing. The testing led to the addition of holes through which to fasten the mount using screws

and a cut-out for placing the steering servo. The topology optimization process is summarized in Fig. 29a.

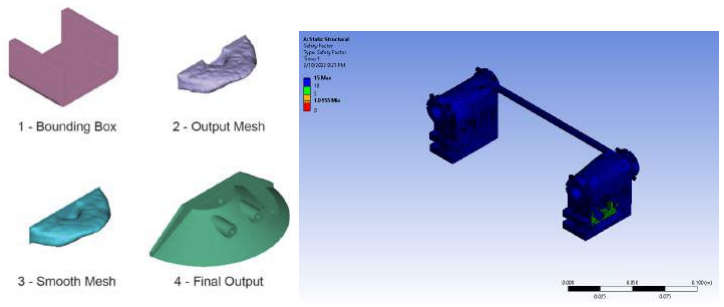
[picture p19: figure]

(a) TO Nose Gear Mount | (b) Rear Landing Gear Mount FEA

Figure 29: Landing Gear Mounts

The rear landing gear mount also saw many iterations. Initially, the rear landing gear was coupled with the rear

pieces of the wing mount. However, upon flight testing, the landing gear was required to move forward in order

to increase the pitching moment to takeoff within 25 ft. In order to keep the wing in the same position relative

to the center of gravity, the landing gear was de-coupled from the wing mount. Fig. 29b shows the validation of the new mount, which was weight-optimized after the results of the simulation indicated the inclusion of excess

material.

### 5.3.9 Tail

The tail design took the shape of a twin boom U-tail as determined in preliminary design. The tail booms were

two 36 in long unidirectional carbon spars that taper from a diameter of 0.83 to 0.485 in to optimize strength

and weight distribution. Constructed similar to the wings, the vertical and horizontal stabilizers are cut to the

shape of the airfoil out of XPS foam. One 0.394 in woven carbon fiber spar was used as the primary structural

Figure 30: Stabilizer Connectors member in the each stabilizer. A short 0.315 in carbon spar was used as an

additional connecting point between the foam and connector. Connecting

the elements of the tail was a 3D printed PLA part that joined tail stabilizers

and booms. Objectives of this part are providing rigid connection between

tail components and a servo wire routing path. Tail booms were inserted into

the connector with servo wires passing though a boom. The connector had

two mounting holes on both the vertical and horizontal stabilizer interface

for spars. FEA was performed on the tail boom spars to verify the rigidity

under maximum aerodynamic load from the tail. The result suggested that

under maximum loading from stabilizers, which was 18 lb on two tail boom, one single tail boom would deflect about 0.5◦
. FEA was conducted on the

connector piece to ensure it’s ability to withstand and transfer the load. Applying loads equal to the maximum

expected aerodynamic forces from the stabilizers, it was found that the connector would maintain a minimum

factor of safety of 3.7, and over 15 for reinforced wire channels, providing sufficient strength.

### 5.3.10 Nose and Empennage

The nose and empennage for the aircraft were similar in design as their primary purpose was for aerodynamics,

as they experience small structural loads. The nose is an 8 in parabolic shape with a filleted square base to

interface with the fuselage cross section. Similarly, the empennage was fitted to the square cross section of the

fuselage at its base, with a 13.02 in length. Both the nose and the empennage, shown in Fig. 31, were attached

using 2 sets of plastic hinges on the top and a locking mechanism on the bottom that was secured using a cotter

pin. The nose also included the pitot tube and a plywood mount for 20 syringes, including an array of netting

hooks to secure the syringes. The material for the nose was selected to be PET plastic which would be vacuum

formed in order to create a durable, lightweight structure; however, the complex shape of the empennage made it

necessary to be 3D printed out of PLA. For the nose and empennage shells, FEA was done on the load bearing

locking mechanisms. The weakest points analyzed were the 3D-printed cotter pin holes that attached to the

fuselage ribs. Using FEA, these locking components were tested over three times the expected weight of the

nose and showed to be durable by two orders of magnitude when analyzing stress.

Figure 31: Nose and Empennage Shells

### 5.3.11 Propulsion

The SMC Graphene Extreme V2 40C battery pack was selected since it was the lightest option and SMC has

the best record of accurate C rating as well as high discharge percentage according to “Real C” battery load

tests performed by MCSGUY on RC Groups (8). In addition, a 160 A fuse was selected to protect the motors

according to data posted by T-Motor (9), since the motors would fail before the battery reaches its maximum

discharge of 180 A. Considering the mechanical and electrical punishment during repeated STOL operations,

the APD 12S 120 A F3[X] ESC was selected for its extreme robustness. Designed for high continuous power

draw of drone racing and surviving high speed crashes, maximum performance and reliability are guaranteed

by this ESC, while being more than 0.2 lb lighter than traditional fixed-wing ESCs.

### 5.4 Aircraft Flight and Mission Performance

Table 17 shows the predicted aircraft performance for each mission using data gathered from previous sections.

Table 17: Predicted Aircraft Performance for each Mission

### 5.5 Weight and Balance

The Albatross’s empty weight is 12.52 lb. The center of gravity is located at the quarter-chord of the wing, which

sits approximately 26 in back from the tip of the nose cone.

Table 18: CG Table with Frame of Reference

### 5.6 Drawing Package

The drawing package contains a dimensioned 3-view of the aircraft, additional views of the primary structure of

the aircraft, locations of the electronics within the aircraft, and detailed views of the subsystems of the aircraft.

17.91 5.29

1

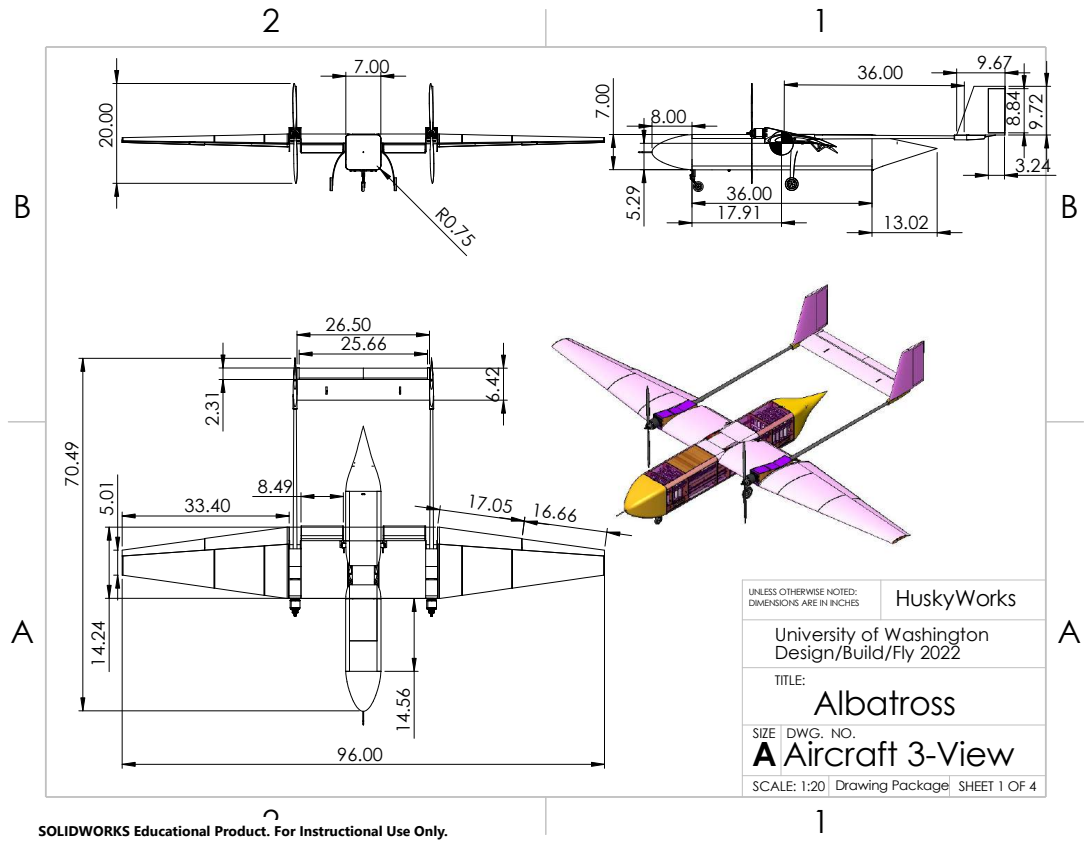
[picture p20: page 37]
DIMENSIONS ARE IN INCHES; HuskyWorks; TITLE:

UNLESS OTHERWISE NOTED:
University of Washington
Design/Build/Fly 2022
Albatross

SIZE A | DWG. NO. Aircraft 3-View

SCALE: 1:20 | Drawing Package | SHEET 1 OF 4

SOLIDWORKS Educational Product. For Instructional Use Only.

B B

2

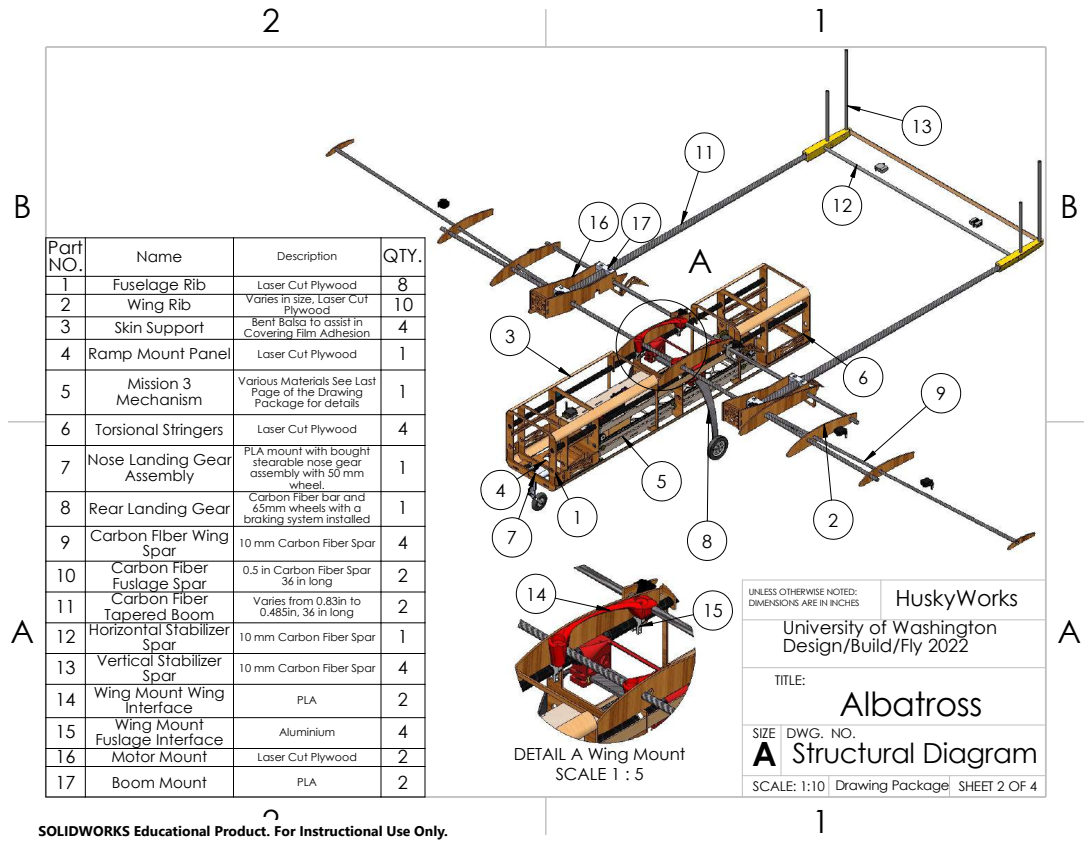
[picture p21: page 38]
TITLE:

Part NO. | Name | Description | QTY.

1 | Fuselage Rib | Laser Cut Plywood | 8
2 | Wing Rib | Varies in size, Laser Cut Plywood | 10
3 | Skin Support | Covering Film Adhesion Bent Balsa to assist in | 4

4 | Ramp Mount Panel | Laser Cut Plywood | 1
5 Mission 3 | Mechanism | Various Materials See Last Page of the Drawing Package for details | 1

6 | Torsional Stringers | Laser Cut Plywood | 4
7 | Nose Landing Gear Assembly | PLA mount with bought stearable nose gear assembly with 50 mm wheel. | 1

8 Rear Landing Gear | | Carbon Fiber bar and 65mm wheels with a braking system installed | 1
9 | Carbon FIber Wing Spar | 10 mm Carbon Fiber Spar | 4
10 Carbon Fiber | Fuslage Spar | 0.5 in Carbon Fiber Spar 36 in long | 2
11 Carbon Fiber | Tapered Boom | Varies from 0.83in to 0.485in, 36 in long | 2
12 Horizontal Stabilizer | Spar | 10 mm Carbon Fiber Spar | 1
13 Vertical Stabilizer | Spar | 10 mm Carbon Fiber Spar | 4
14 Wing Mount Wing | Interface | PLA | 2
15 Wing Mount | Fuslage Interface | Aluminium | 4

UNLESS OTHERWISE NOTED: DIMENSIONS ARE IN INCHES | HuskyWorks

University of Washington
Design/Build/Fly 2022
Albatross

SIZE A | DWG. NO. Structural Diagram

16 | Motor Mount | Laser Cut Plywood | 2
17 | Boom Mount | PLA | 2

DETAIL A Wing Mount
SCALE 1 : 5

SCALE: 1:10 | | SHEET 2 OF 4 Drawing Package

SOLIDWORKS Educational Product. For Instructional Use Only.

B B

2

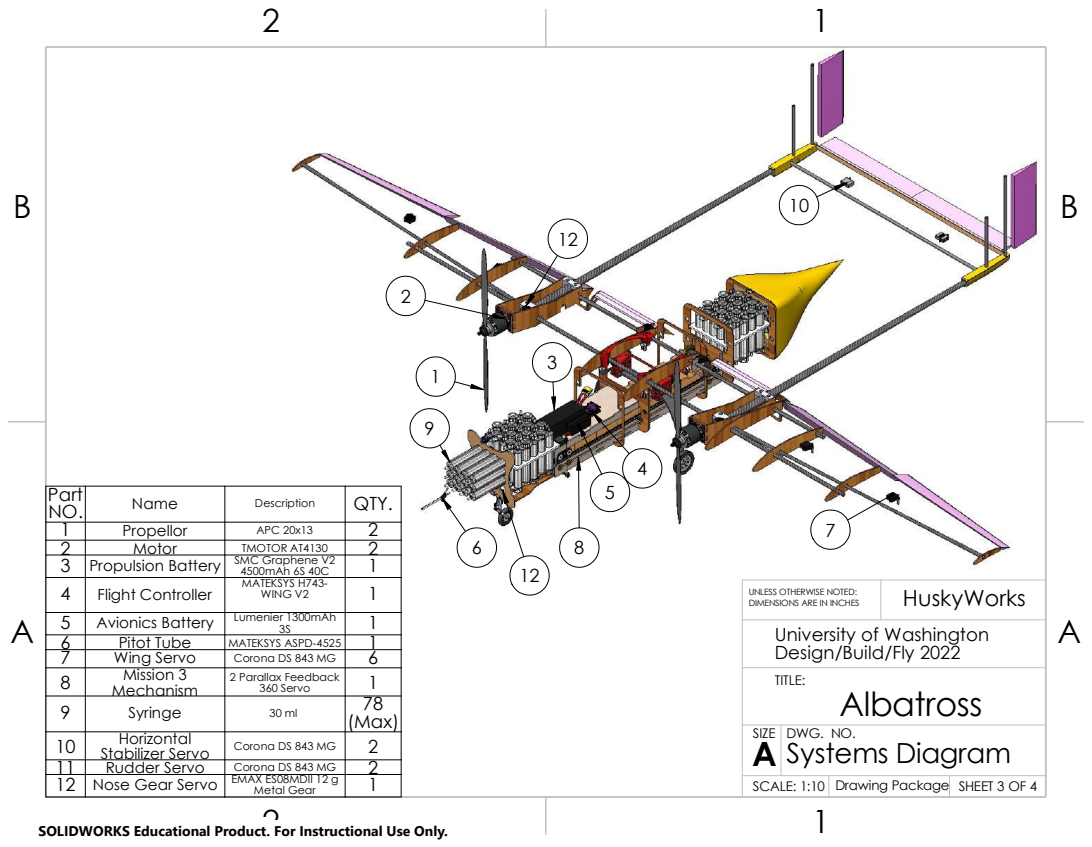
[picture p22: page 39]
TITLE:; SCALE: 1:10; SHEET 3 OF 4 Drawing Package; HuskyWorks; 4 Flight Controller; MATEKSYS H743-; WING V2; 8 Mission 3 Mechanism; 2 Parallax Feedback; 360 Servo; Nose Gear Servo; EMAX ES08MDII 12 g; Metal Gear

Part NO. | Name | Description | QTY.

1 | Propellor | APC 20x13 | 2
2 | Motor | TMOTOR AT4130 | 2
3 | Propulsion Battery | SMC Graphene V2 4500mAh 6S 40C | 1

UNLESS OTHERWISE NOTED:
DIMENSIONS ARE IN INCHES
University of Washington
Design/Build/Fly 2022
Albatross

5 | Avionics Battery | Lumenier 1300mAh 3S | 1
6 | Pitot Tube | MATEKSYS ASPD-4525 | 1
7 | Wing Servo | Corona DS 843 MG | 6

9 | Syringe | 30 ml | 78 (Max)

SIZE A | DWG. NO. Systems Diagram

10 Horizontal | Stabilizer Servo | Corona DS 843 MG | 2

11 | Rudder Servo | Corona DS 843 MG | 2

SOLIDWORKS Educational Product. For Instructional Use Only.

B B

2

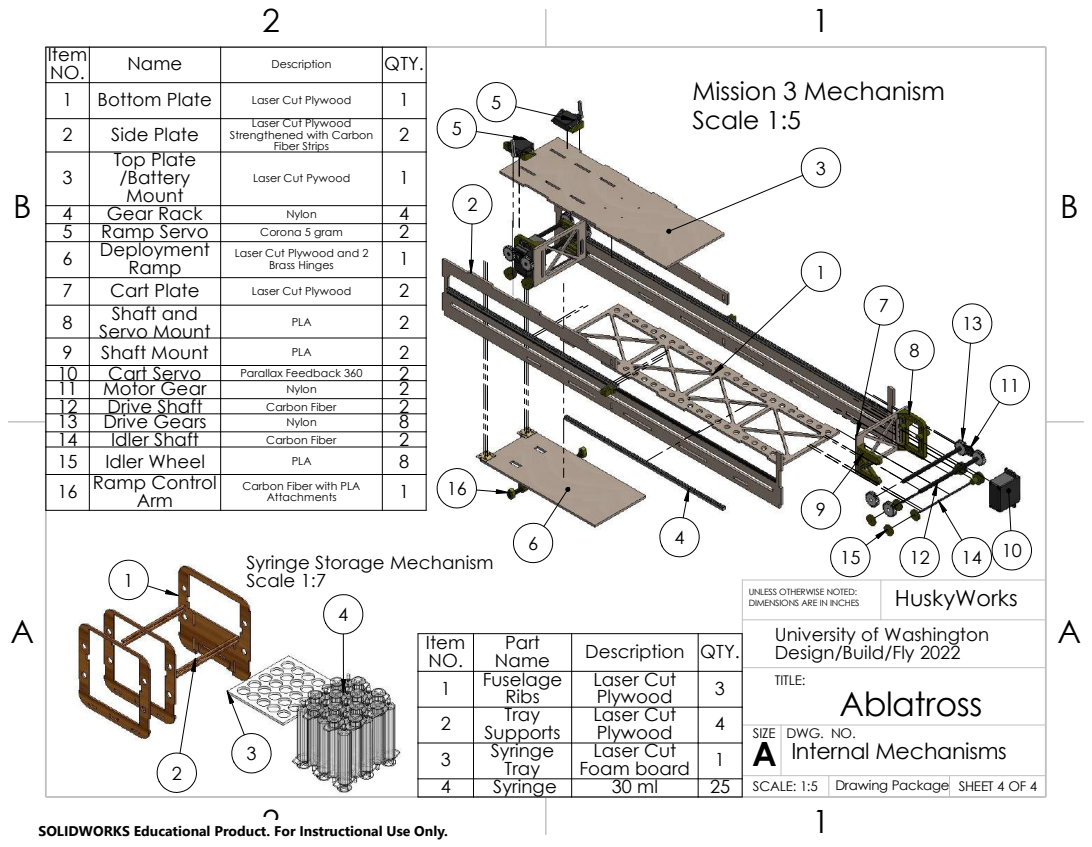
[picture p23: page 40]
TITLE:; HuskyWorks; Mission 3 Mechanism Scale 1:5

Item NO. | Name | Description | QTY.

1 | Bottom Plate | Laser Cut Plywood | 1

2 | Side Plate | Laser Cut Plywood Strengthened with Carbon Fiber Strips | 2
3 | Top Plate /Battery Mount | Laser Cut Pywood | 1

4 | Gear Rack | Nylon | 4
5 | Ramp Servo | Corona 5 gram | 2
6 Deployment | Ramp | Laser Cut Plywood and 2 Brass Hinges | 1

7 | Cart Plate | Laser Cut Plywood | 2
8 | Shaft and Servo Mount | PLA | 2
9 | Shaft Mount | PLA | 2
10 | Cart Servo | Parallax Feedback 360 | 2
11 | Motor Gear | Nylon | 2
12 | Drive Shaft | Carbon Fiber | 2
13 | Drive Gears | Nylon | 8
14 | Idler Shaft | Carbon Fiber | 2
15 | Idler Wheel | PLA | 8
16 Ramp Control | Arm | Carbon Fiber with PLA Attachments | 1

Syringe Storage Mechanism
Scale 1:7

UNLESS OTHERWISE NOTED:
DIMENSIONS ARE IN INCHES
University of Washington
Design/Build/Fly 2022
Ablatross

Item NO. | Part Name | Description | QTY.
1 | Fuselage Ribs | Laser Cut Plywood | 3
2 | Tray Supports | Laser Cut Plywood | 4
3 | Syringe Tray | Laser Cut Foam board | 1

SIZE A | DWG. NO. Internal Mechanisms

4 | Syringe | 30 ml | 25 | SCALE: 1:5 | SHEET 4 OF 4 Drawing Package

SOLIDWORKS Educational Product. For Instructional Use Only.

## 6 Manufacturing Plan

### 6.1 Manufacturing Processes Investigated

### 6.1.1 Composites

The use of composite materials such as carbon fiber has commonly been considered for design constraints in

which a material with high specific strength would be optimal. While composite layups for parts such as wings

and fuselage would allow for the aircraft to undergo greater load before failure, the downsides of increased time,

cost, and complexity associated with a wing/fuselage make it improbable for use in some applications.

### 6.1.2 Laser-Cutting

Laser cutting is ideal for projects requiring quick precise 2D cuts of thin wood and foam. It is ideal for the use of

structural bulkheads and ribs, as well as for hotwire cutting stencils. Laser cutting is not ideal for 3D parts with

complex geometry.

6.1.3 3D-Printing

3D printing allows for the physical prototyping and manufacturing of 3D CAD models. Often used for topologically

optimized parts, 3D printing allows the team to manufacture parts with complex geometry. The quality and

integrity of 3D printed structures are influenced by the type of filament, the slicer settings used for the print, and

the print orientation.

### 6.1.4 Covering Film

Covering film, combined with the use of plywood and balsa wood, can be used to make light-weight structures for

both the fuselage and wings. An iron can be used to shrink and adhere the film to the wood, creating a smooth

surface for aerodynamics.

### 6.1.5 Hotwire-Cutting

The hot wire cutter operates by sending a current through a thin strand of wire which generates heat. This is

a cheap and time-efficient way to shape XPS foam and other similar materials. This year, the team explored

the use of a CNC hotwire cutter, which would automate the process done previously by hand. Additionally, the

minimal experience needed to operate the hotwire cutters is ideal. All of these benefits yield hotwire cutting to

be one of HuskyWorks’ primary manufacturing methods.

### 6.1.6 Machining

The use of a manual mill or lathe can be used to produce high-tolerance parts. This technique allows for pro-

cessing of other high strength materials at the cost of large setup times.

### 6.1.7 Vacuum Forming

Vacuum Forming PET plastic was used to manufacture lightweight parts with little structural loads. The process

heats up thin plastic sheets while a mold is pushed through. When the part cools down, it creates thin, somewhat

flexible shells.

### 6.2 Manufacturing Processes Selected

Fig. 32 shows the materials used in the construction of the Albatross. Materials and manufacturing processes

were selected based on available resources, cost, time, and complexity.

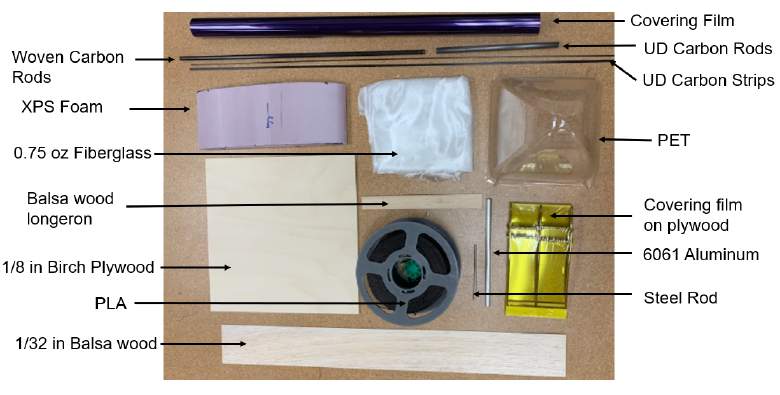
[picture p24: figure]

Figure 32: Albatross Materials Selected

### 6.2.1 Fuselage

The fuselage was constructed with a combination of birch plywood bulkheads, balsa wood stringers, covering

film, and carbon fiber rods. Two unidirectional carbon fiber rods ran the length of the fuselage, interfacing with

laser cut bulkheads placed in high stress areas. The main shape of the fuselage was formed by covering film

heat-shrunk around the ribs and stringers. Ribs were laser cut from 1/8 in birch plywood, and secured into posi-

tion on 1/2 in carbon fiber rods using glue. During assembly of the fuselage, the wing mounts and landing gear

mounts which interface with the spars were slid into place and glued or clamped.

To support the covering film on the corners of the fuselage, stringers were made of balsa wood and layered with

fiberglass to provide extra bending resistance and a surface for the film to adhere to. This prevented the covering

film from curving inwards on the corners of the fuselage when shrunk, improving the aerodynamic streamline of

the fuselage as a whole. Stringers were bent into a rounded shape to follow the curvature of the fuselage using

a jig created with a carbon fiber rod and laser cut birch plywood rings shown in Fig. 33a. Water was applied to a

1/32 in sheet of balsa using a paper towel, and the sheet was then bent to shape around the plywood rings. The balsa was held in the curved position using a tightened nylon string. After 2 hours of drying, the balsa was cut

to shape using a knife, and 0.75 oz fiber glass was applied via a wet layup. Once the stringers were completely

dry and the fiber glass had set, they were cut to size and secured to the fuselage using polyurethane glue. The

next step in the process was to heat shrink the covering film around the fuselage; however, due to a need to

access electronics and the deployment mechanism, this step was performed just before systems checks.

(a) Stringer Jig | (b) Covering Film Fuselage | (c) Internal Structure

Figure 33: Fuselage Manufacturing Process Images

### 6.2.2 Wing and Tail

The general process for the construction of wing sections for the Albatross was using laser cut wooden stencils

and a hotwire to cut wing sections out of XPS foam into the desired wing shape. Laser cut wooden ribs and

carbon fiber spars were inserted into the foam to provide the necessary structure in the wing. Fiberglass was

laid up on the wing to provide torsional rigidity.

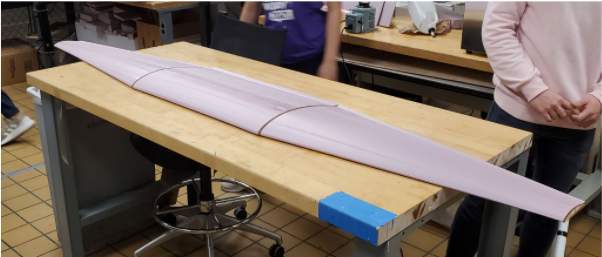
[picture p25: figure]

Figure 34: Contoured Foam Wing Sections

The wing was made in three sections: left, center, and right. The center wing section was constructed in a multi-

step process starting with laser cutting 2, 1/8 in birch plywood stencils to the shape of the selected airfoil and

gluing the stencils to a 2 in piece of foam sized for the center section. A manual hotwire cutter was used to cut

the foam to the shape of the stencils. Channels for wires were cut after the aerodynamic shape was completed.

Figure 35: Center Wing Section with Mount

The center section was cut into three shapes to insert

the wing mount. A bandsaw-style hotwire cutter was

used to cut holes for the mount. The mount was glued

to a wooden rib in the foam. Fiberglass was laid up

onto the surface after the mount was inserted. Fig. 35

shows the completed center section wing mount. The

wing section was placed in a vacuum bag as shown

in Fig. 36 to cure for two hours to obtain a smooth

surface finish and remove excess resin. To complete

the assembly of the center wing section, carbon fiber spars were glued into position in the ribs and wing mount,

and motor mounts were glued on to the outer edges of the wing section. The left and right wing were built using

the same process as the center section, with additional challenges due to the taper. When hot wire cutting these

sections, two different sized stencils were used to obtain the desired taper angle. When cutting using these

stencils, one side of the hotwire was moved at a different speed than the other to ensure a smooth, even cut

was made. General control surfaces were made using a hotwire cut foam core layered in 1/32 in balsa wood

adhered to the surface using spray adhesive. Control horns were laser cut from 1/8 in birch plywood and a slot

for the horn was cut into the surface using a hand held foam cutting tool. The control horns were then glued into

place using polyurethane glue. The slotted flaps were constructed using a laser cut 1/8 in birch plywood rib on

either side with a foam core hotwire cut to the correct contour spanning between the ribs.

Figure 36: Vacuum-bagged Wing

The main shapes of the vertical and horizontal stabilizers were cut using a hotwire cutter and stencil method simi-

lar to the method used to cut wing sections. 3D printed pieces served as the joints between the foam surfaces cre-

ating the Albatross’s U-shaped tail. Carbon fiber rods were inserted into channels cut with the hotwire to provide

(a) Slotted Flaps | (b) Tail Assembly

Figure 37: Control Surfaces and Tail Assembly structure to the foam pieces and serve as

the backbone of the tail structure. The

rudders on the tail were controlled us-

ing Kevlar strings connected to servos

mounted on the main wing section in the

motor mounts. Channels for wires and

holes for servo motors were cut using a

Dremel tool with a router attachment.

### 6.2.3 Aerodynamic Cowlings

The primary aerodynamic cowlings on the Albatross were the nose and empennage. Both of these cowlings

were made of with a combination of vacuum formed PET plastic and 3D printed PLA. The tip of the nose cone

was made of vacuum formed plastic while the rest of the nose was made of 3D printed PLA. The empennage

was entirely 3D printed. Slicer settings were changed for the nose and empennage prints to get a single layer

thick print with no infill, significantly reducing the weight of the part. In both the nose and empennage, holes

were drilled for screws to mount hinges connected to the fuselage. 3D printed latches were also attached using

polyurethane glue to the nose and empennage to secure them to the fuselage in conjunction with the hinges.

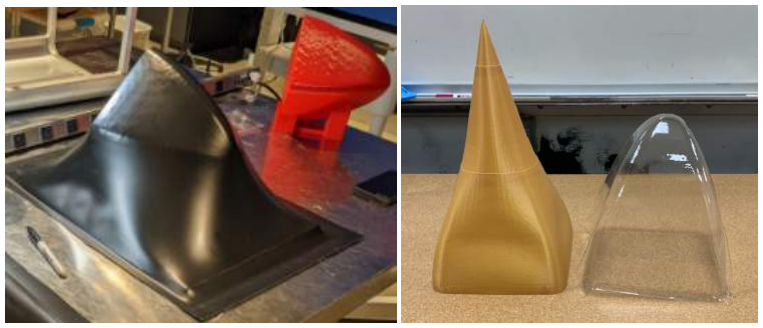
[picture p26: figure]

(a) Vacuum Forming | (b) Nose and Empennage
Figure 38: Aerodynamic Cowlings

### 6.2.4 Mounts

The motor mounts were laser cut out of 1/8 in plywood and glued together using spars as alignment. The wing

mount was made in multiple parts out of both PLA and 6061 aluminum. The mount inserted into the foam was

3D printed. The mounts secured to the fuselage longerons were fabricated using a manual mill.

(a) Machining Process | (b) Installed Aluminum Mount

Figure 39: Aluminum Wing Mount Manufacturing

### 6.2.5 Payload & Deployment Mechanism

The Mission 3 deployment mechanism was laser cut out of 1/8” plywood and glued together using epoxy. Uni-

directional carbon strips were glued along the span in the vertical and horizontal directions to provide stiffness.

Figure 40: Payload Deployment Mechanism Frame and Package Handling Carts

### 6.2.6 Aircraft

Fig. 41 shows the first version of team HuskyWork’s competition airframe at it’s first test flight.

Figure 41: Competition Aircraft Version 1

### 6.3 Manufacturing Schedule

Manufacturing of the Albatross was structured to be simple and easily repeated. With the planned construction

of three aircraft: the Aerodynamic Prototype, Competition Version 1, and Competition Version 2, scheduling was

mirrored from one airframe to the next. This allowed for consistent weekly schedules to keep manufacturing on

time, and for processes to be streamlined and improved for each iteration of aircraft. A Gantt chart depicting the

detailed manufacturing timeline is shown in Fig. 42. It should be noted that the chart includes the time taken to

build the part for the first prototype, iterate and improve the design, and build it for the subsequent aircraft.


Figure 42: Manufacturing Timeline Gantt Chart

## 7 Test Plan

### 7.1 Test Schedule

Figure 43: Testing Timeline Gantt Chart

### 7.2 Testing Objectives

The following section presents bulleted lists of testing objectives for various components of design.

### 7.2.1 Aerodynamics

- The Aerodynamic Prototype served to validate the results of the stability analysis.

– Pilot feedback coupled with on-board black box data from the flight controller was used to verify

airspeed, stability and maneuverability

– An FPV camera and video transmitter provider the pilot with live airspeed data

- Wind tunnel testing was performed to determine the aerodynamic properties of the design such as lift,

drag, moment, and stall/cruise conditions.

### 7.2.2 Structures

- Cantilever, point-load beam tests, and structural demonstrations were used to validate the results of the

FEA of the fuselage, wing, and relevant internal mounts.

- A pre-flight wingtip test was used to verify the airframe structure and simulate technical inspection.
- Tests during flight will be performed to verify the structural limits of the aircraft during high-G maneuvers,

takeoff, and landing.

### 7.2.3 Propulsion

- The preliminary propulsion system was tested to demonstrate satisfactory performance during all phases

of each flight mission.

### 7.2.4 Payload

- A fuselage drop test was performed including a vaccine package to verify that the 25G shock sensor would

not trip upon an impact force, such as landing.

- Extensive mechanical testing was performed on the Mission 3 deployment mechanism to guarantee relia-

bility of electronics and code.

- Mission 2 and 3 flight simulation test will be performed to verify aircraft performance for STOL with maximum

payload and repeated takeoffs and landings.

### 7.3 System Testing

### 7.3.1 Aerodynamics Testing

Tests were performed in a 3 ft x 3 ft wind tunnel to test the aerodynamic properties of the designed body including

lift, drag, and pitch moment. The test model was 3D printed with PLA, PETG, and PC, sanded and reinforced

with aluminum and steel spars. In order to better simulate free-flight within the limited size of the wind tunnel,

a 50% scale, half-body design was chosen. Given the scale model, the Reynold’s number estimated for M3

conditions was matched. The half-body was mounted with its xz-plane (body axes) cut plane parallel to the

tunnel floor, attaching to the ATI Mini 45-E balance and rotation table allowing for angle of attack variation. The

tested angles of attack were between −5

- and 12.5

◦
. Yaw and roll variations were not tested.


(a) (b)

Figure 44: (a) Airframe half-body mounted vertically in wind tunnel and (b) motor-propeller propulsion test apparatus

The CD measured in the wind tunnel did not match results from AVL and OpenVSP, as seen in Fig. 10a. Dur-

ing flow-on testing, the measured axial force was lower than expected relative to the tare value and suggested potential contact between the model-attached fairing under the splitter plate and the tunnel floor due to installed

tolerances. In Fig. 10b, the lift-to-drag curve was observed to have a similar slope compared to AVL and Open-

VSP. This was seen as a correct prediction, as the slope of the drag polar seen in Fig. 10a is L/D, meaning

that the lower slope would translate to a lower α vs. L/D curve.

The effects of the endplates were observed to be minimal on the CL of the plane, as seen in Fig. 11. Endplate

(c) exhibited a lower slope, but it was noted in the data that the axial force tare was significantly lower than the

previous cases, this difference in axial force impacting the CL for the endplate (c) curve. Based on the error

present in taking α values due to low tolerances of the force balance turning mechanism, it was deemed that

there would be little benefit to choosing an endplate design based on the available data.

### 7.3.2 Propulsion Testing

Wind Tunnel Testing

To compare against performance predicted by eCalc, max power performance of the T-Motor AT4130 300 KV

and APC 20X13E prop was measured in the wind tunnel. Thrust and torsion were measured with respect to

airspeeds from 0 to 88.58 ft/s, supplying aircraft performance calculations and motor mount design with more

accurate data.

In-Flight Testing

Flight tests were conducted to evaluate the overall performance of the propulsion system if calculations based on

wind tunnel data suggest they were feasible. Mission simulations and various flight scenarios were conducted

to obtain data from the field and from telemetry.

### 7.3.3 Structural Testing

A wing structure test was designed to validate the finite element analysis performed on the wing structure through

testing to the max loading condition that the wing could experience (2.5G wing tip load). Due to the complexities

of the tapered spars, the FEA could not generate reliable results for realistic loading cases. One outer wing

section, identical to that of the competition aircraft, was constructed for this test. The outer wing was selected

due to the fact that it only included one carbon fiber spar, indicating that it was the weakest part of the wing in

terms of bending rigidity. Additionally, due to the taper, the wing tip is more critically loaded in shear.

The test performed was an incremental static loading test. The first objective of this test was to record the degree

of deflection of the wing for multiple applied loads. The second objective of this test was to test if this wing section

could withstand and recover from load equal to 2.5G at wing tip. A test stand was constructed to secure the wing

section in place such that it extrudes over the edge of a table. A bucket was attached to the tip of the wing and

water was poured into the bucket in 4 oz increments.

### 7.3.4 Package Deployment Mechanism Testing

Figure 45: Mission 3 Testing: 2 Packages

During Mission 3, the package deployment mecha-

nism must reliably deploy packages quickly without

getting jammed. To ensure the reliability and speed

of the deployment mechanism, the mechanical parts

of the deployment mechanism were tested as shown

in Fig. 45. The mechanical design of the package

handling carts was tested using a very simple method.

The package handling carts were mounted inside the

frame and connected to a servo tester. A PWM control

signal was manually sent to the package handling cart

via the servo tester such that the carts would travel

along the frame in either direction. This method of testing was used to verify proper gear meshing and smooth

movement of the package handling carts. The servos were also tested for adequate performance by pushing

a weight of 3 lb (six packages worth of weight) along the length of the frame. This would verify that the servo

could indeed push the boxes the desired speed without stalling.

### 7.4 Flight Tests

### 7.4.1 Flight Test Airframes

Three design iterations were used to evaluate the flight performance of the Albatross, as summarized in Tables

19 and 20. Using multiple airframes of increasing capability allowed both lessons from the test flight program

and improvements in the manufacturing process to be included in the final design.

Table 19: Airframe Features


(a) Aerodynamic Prototype in Flight | (b) Competition V1 in Flight

Figure 46: Airframes in Flight

Table 20: Airframes Tested

### 7.4.2 Flight Test Schedule

Table 21: List of Flight Test Objectives

* A flight is defined as the use of one battery, not takeoff and landing cycles

### 7.4.3 Flight Checklist

Table 22: Pre-flight Checklist

## 8 Performance Results

### 8.1 Demonstrated System Performance

### 8.1.1 Propulsion Testing Results

The graph shown in Fig. 47 was produced from the results of the wind tunnel thrust test.

Figure 47: T-Motor AT4130 300 KV + APC 20X13E Dynamic Thrust Performance at 3000 Watts

While the M2 thrust performance is satisfactory, according to Fig. 47, an 18% average thrust deficit to eCalc

predictions was measured during the takeoff regime from 0 to 40 ft/s. Since the AT4130 was the most powerful

of its class, it was deduced that other motors may suffer the same deficit. With larger motors requiring significant

structural changes, the AT4130 was elected to continue flight test to progress other testing programs, while a

backup solution was investigated in case more thrust was needed.

General flight performance and M3 performance were both evaluated directly by conducting flight tests. The pilot

was instructed to fly under 900 Watts of power after takeoff, with average airspeed, and flight time (excluding

landing sequence) recorded. 3 flights were conducted in this manner, with an average airspeed of 42 ft/s and

an average flight time of 6 minutes 48 seconds. Distance equivalent to 8 competition laps was obtained through

conservative calculations. Since all flights landed with at least 15% propulsion energy remaining, enough to

account for energy consumption of 6 takeoffs, M3 propulsion performance was considered satisfactory. Pilot

feedback was positive on the responsiveness and acceleration provided by propulsion, and zero failures were

suffered by the APD ESCs after more than 30 takeoffs and landings. Lastly, during flight test of Competition V1,

takeoff within 25 ft was achieved using the AT4130 motor at half payload with more than 3 ft to spare. Since

takeoff performance is expected to improve on Competition V2 with better landing gear placement, combined with

calculations, takeoff performance from the AT4130 was considered sufficient. Therefore, due to their satisfactory

performance, all components from preliminary propulsion design were finalized.

### 8.1.2 Structural Testing

Figure 48: Max Wing Deflection (20◦ )

Given an applied load of 13.1 lb added incrementally, the wing deflected 15◦ without any visible structural damage. This test

simulated the bending moment at the inboard side of the wing,

validating the structure’s ability to withstand this load. After this

was validated, the wing was loaded up to 18.75 lb to simulate a 2.5G wing tip load. The wing was observed to deflect 20◦ with a

tip displacement of -10 in, as shown in Fig. 48. Upon inspection

of the wing, minimal damage was observed.
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

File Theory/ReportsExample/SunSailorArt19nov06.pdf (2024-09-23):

1

## SunSailor: Solar Powered UAV

Faculty of Aerospace Engineering, Technion IIT, Haifa, Israel, Students’ Project

A. Weider, H. Levy, I. Regev, L. Ankri, T. Goldenberg, Y. Ehrlich, A. Vladimirsky,
Z. Yosef, M. Cohen.
Supervisor: Mr. S. Tsach, IAI

ABSTRACT
This paper summarizes the final project of undergraduate students' team at the Faculty of Aerospace Engineering at the Technion IIT, Haifa, Israel. The team was formed to design, build, test and fly a Solar Powered Unmanned Aerial Vehicle with the final goal of breaking the world record for distance flight under certain limitations. Until this moment two UAVs were built at the Technion Workshop. The first flew its first solar flight on June 29th 2006. It crashed on its third solar flight. The second was built in

### 54 days, flew and crashed on its maiden

solar flight. The third UAV was completed lately and had 2 successful flight tests.
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

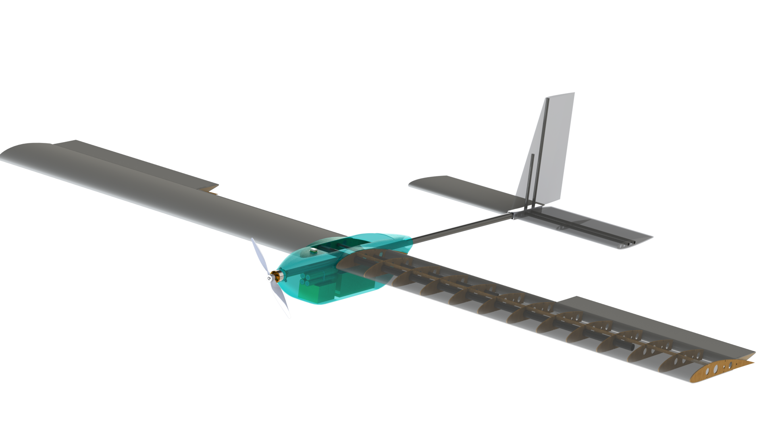
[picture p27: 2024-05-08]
PreliminaryDesign/Images/ViewWithMotor.png

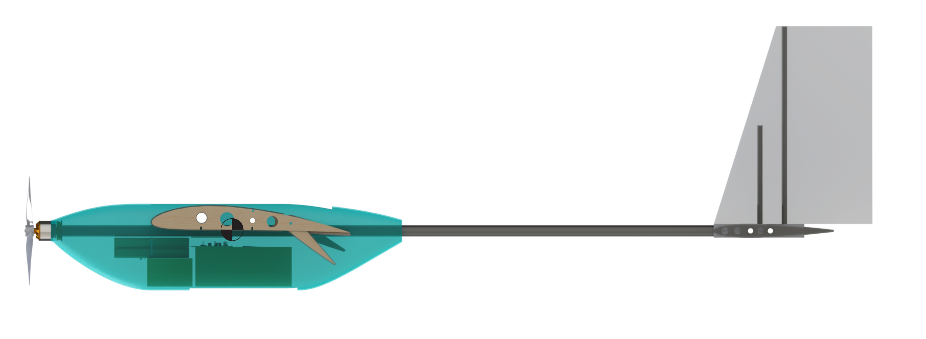
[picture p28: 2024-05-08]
PreliminaryDesign/Images/SideViewTransparentWithCGRealystic.png

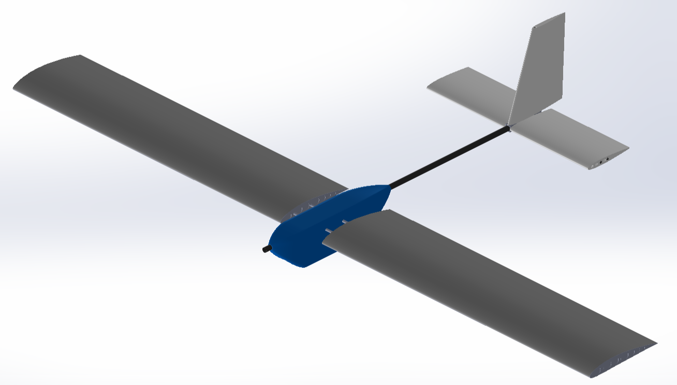
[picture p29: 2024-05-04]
PreliminaryDesign/Images/GeneralViewFirstPrororype.png

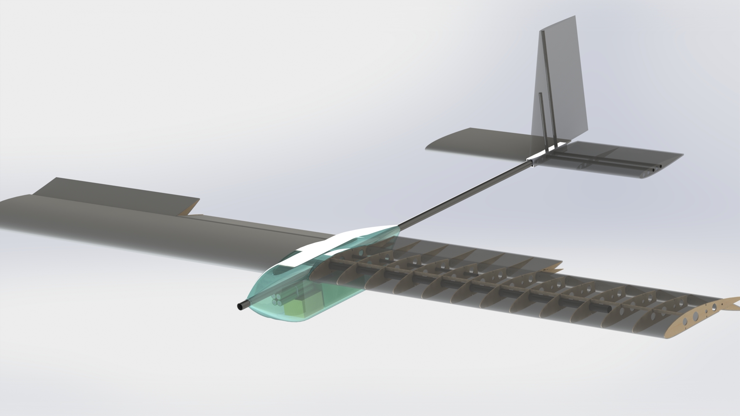
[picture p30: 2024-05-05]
PreliminaryDesign/Images/previewRealisticTransparent.JPG

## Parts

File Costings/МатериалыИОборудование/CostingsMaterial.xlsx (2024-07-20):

Смета |  |  |  |  |  |  | Комменарии
№, п/п | Наименование работ/материалов | продавец | ед. изм. | кол-во | стоимость | сумма
1 | Батареи Molicel 18650 | ozon (https://www.ozon.ru/product/akkumulyator-18650-litiy-ionnyy-li-ion-nizkotemperaturnyy-3-6v-molicel-inr-18650-p28a-706164938/) | шт | 16 | 778 | 12448 ₽
2 | Сервоприводы Suprass Hobby SJ0015H | aliexpress (https://aliexpress.ru/item/1005005753153882.html?sku_id=12000034230242071) | шт | 6 | 1820 | 10920 ₽
3 | Воздушный винт | aliexpress (https://aliexpress.ru/item/1005001659252232.html?sku_id=12000017019512935) | шт | 2 | 489 | 978 ₽
5 | Мотор | aliexpress (https://aliexpress.ru/item/32691417055.html?sku_id=60537385416) | шт | 1 | 3085 | 3085 ₽
6 | Регулятор оборотов | aliexpress (https://aliexpress.ru/item/32655256635.html?sku_id=12000032898861998) | шт | 1 | 2582 | 2582 ₽
7 | Пенопласт | leroymerlin.ru | шт |  |  | 0 ₽
8 | Трубки углепластиковые 7mmх1000mm | fasrshop.ru | шт |  |  | 0 ₽
9
9.54491018 | Лыжные палки | yandexmarket | шт |  |  | 0 ₽
10 | Клей | leroymerlin.ru | шт |  |  | 0 ₽
11.37724551 |  |  |  |  |  | 0 ₽
11 |  |  |  |  |  | 0 ₽
12 |  |  |  |  |  | 0 ₽
13 |  |  |  |  |  | 0 ₽
14 |  |  |  |  |  | 0 ₽
15 |  |  |  |  |  | 0 ₽
16 |  |  |  |  |  | 0 ₽
17.79041916 |  |  |  |  |  | 0 ₽
17 |  |  |  |  |  | 0 ₽
19.62275449 |  |  |  |  |  | 0 ₽
18 |  |  |  |  |  | 0 ₽
19 |  |  |  |  |  | 0 ₽
20 |  |  |  |  |  | 0 ₽
21 |  |  |  |  |  | 0 ₽
22 |  |  |  |  |  | 0 ₽
Итог |  |  |  |  |  | 30013 ₽

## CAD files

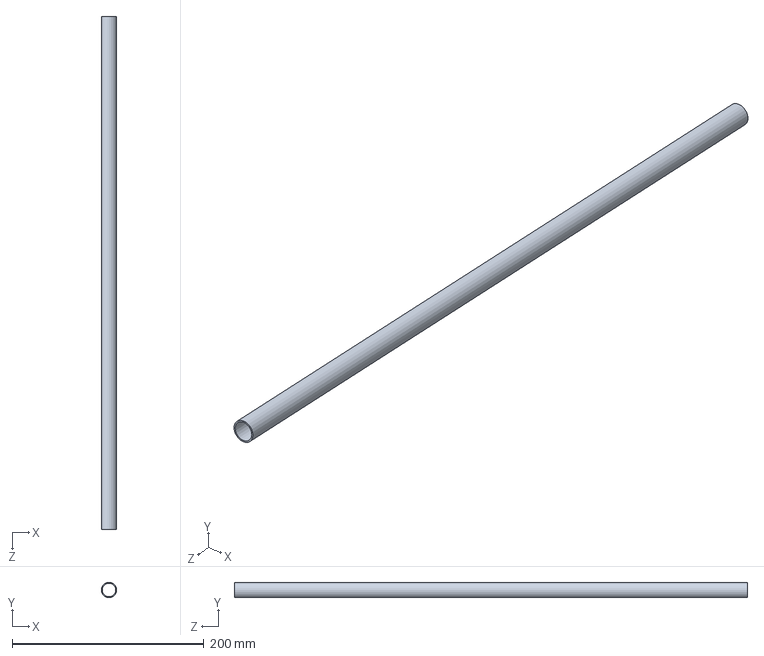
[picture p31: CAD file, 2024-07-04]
Manufacturing/ДетальнаяМодель/МоделированиеFlowSimulation/mainspar.SLDPRT
16.0 x 16.0 x 535.0 mm

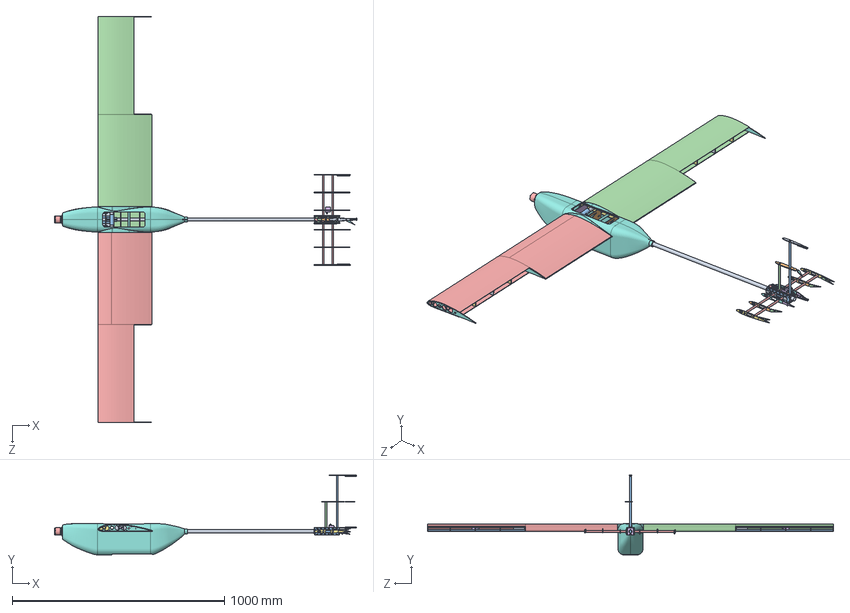
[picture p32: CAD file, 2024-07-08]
ПроизводственныйОтчет/ДетальнаяМодель/Модель/ТекущаяСборка/Сборка_Copy.SLDASM
1424.3 x 376.1 x 1912.2 mm
Treker.step
BatteryHolder x 2
18650 Li-Ion.step x 8
cargo
Sunnysky_2814_BrushlessMotor
Servo x 4
ESC60A
Fuselage_Copy
TailStick
CrossSection4 x 2
CrossSection6
CrossSection7
CrossSection2
CrossSection3
RootRib x 2
WingSparD10mmL1.0m
WingSparD16mmL1.2m
MotorMount
Connector
Aileron170mmNACA0010 x 4
D8mm x 2
ServoAileron170mmNACA0010 x 2
Rib170mmNACA0010 x 2
ServoAileronRib170mmNACA0010 x 2
AileronRootRib170mmNACA0010 x 2
AileronRib170mmNACA0010 x 2
TailConnector x 2
TailConnectorCup
TailConnectorFront
TailConnectorFrontSecond
RudderFin130mm
RudderFin166mm
nerv_fin_130
nerv_fin_166.4
MainSparVerticalTail
AdditionalSparVerticalTail
ServoRib_fin_200
RudderServo
LightAileronRib250mm x 4
LightRib250mm x 10
LightServoRib250mm x 2
stick x 8
Stick2 x 8
XPSEnclosure
XPSEnclosureLeft

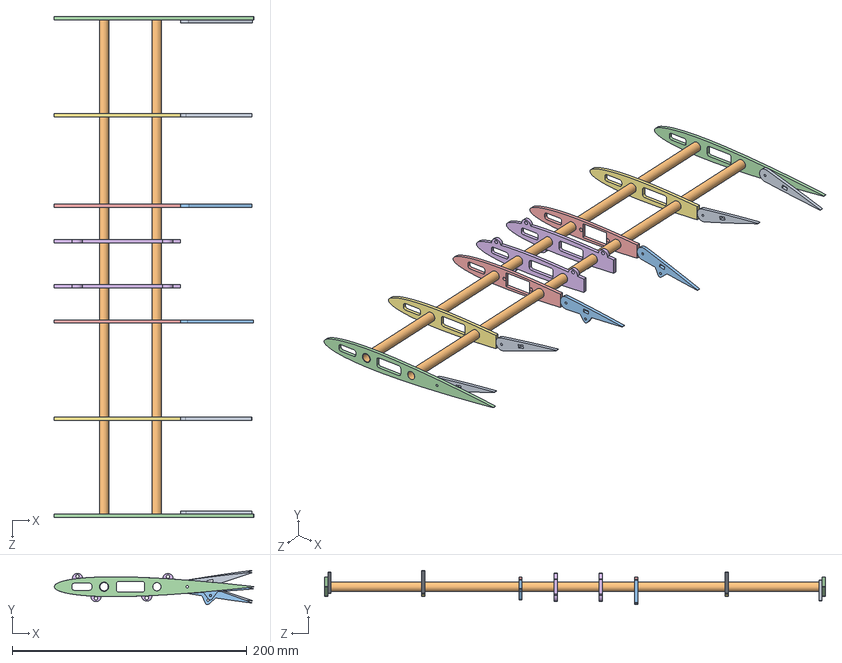
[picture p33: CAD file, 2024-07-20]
Manufacturing/ДетальнаяМодель/Модель/ТекущаяСборка/HorizontalTail.SLDASM
170.1 x 29.2 x 427.0 mm
Aileron170mmNACA0010 x 4
D8mm x 2
ServoAileron170mmNACA0010 x 2
Rib170mmNACA0010 x 2
ServoAileronRib170mmNACA0010 x 2
AileronRootRib170mmNACA0010 x 2
AileronRib170mmNACA0010 x 2

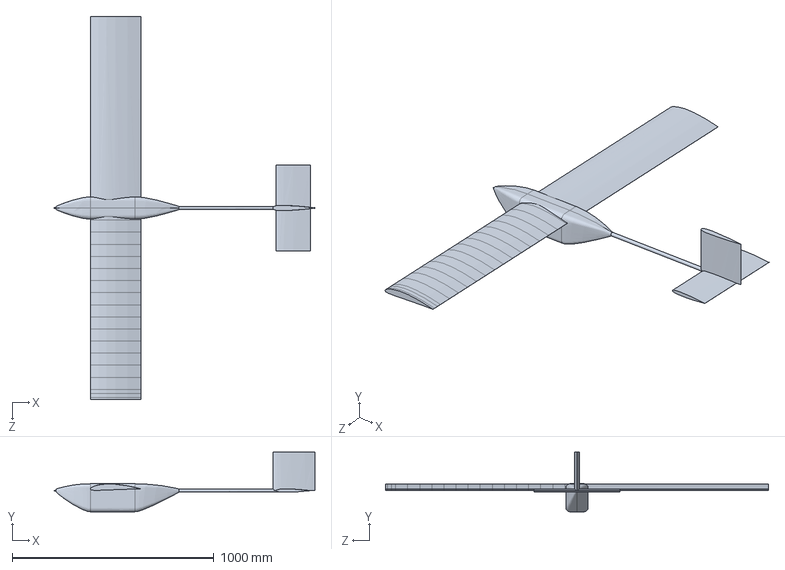
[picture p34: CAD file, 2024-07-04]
Manufacturing/ДетальнаяМодель/МоделированиеFlowSimulation/Assembly.SLDASM
1292.7 x 295.4 x 1900.0 mm

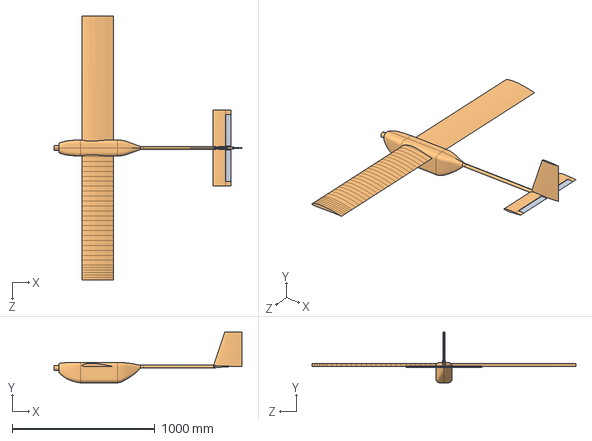
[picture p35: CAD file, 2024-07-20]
Manufacturing/ДетальнаяМодель/МоделированиеFlowSimulation/SD7032/SD7032Assembly.SLDASM
1314.0 x 355.2 x 1850.0 mm
ELEVATOR x 2
TestSD7032

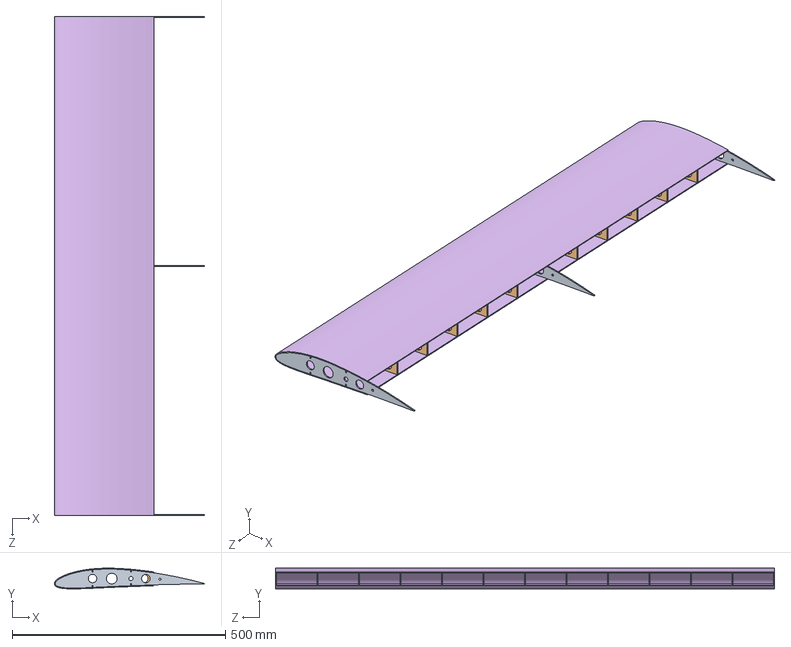
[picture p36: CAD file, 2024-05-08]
PreliminaryDesign/DetailedModel/Wing/WingAssemblyFinal.SLDASM
352.2 x 48.8 x 1169.2 mm
polywoodRib350mm x 3
polywoodAileronRib350mm x 10
polywoodStringer x 11
PolywoodSparRoot
PolywoodSparRoot1
WingEnclosureXPS

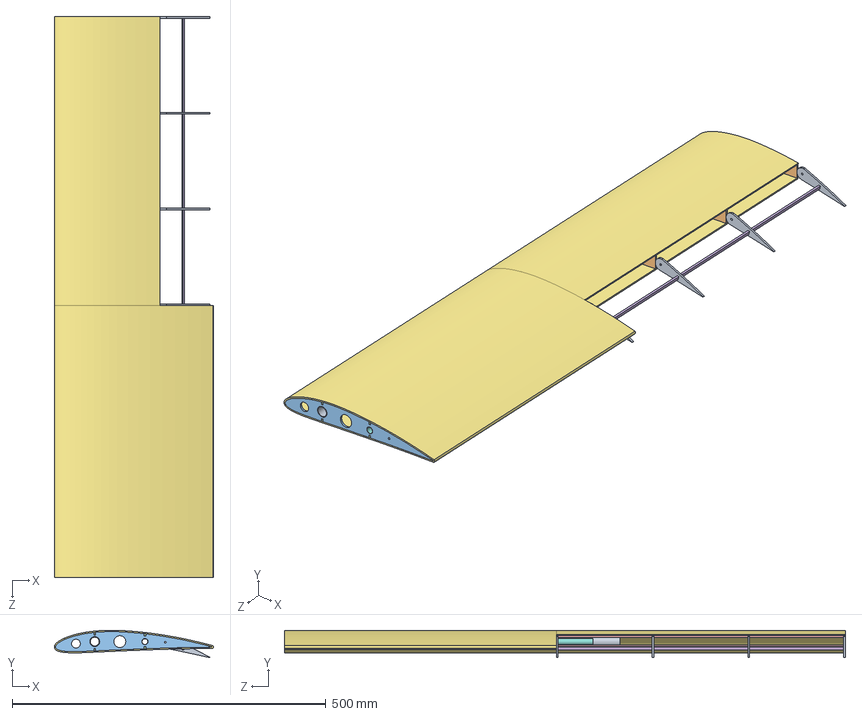
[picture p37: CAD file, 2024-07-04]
Manufacturing/ДетальнаяМодель/МоделированиеFlowSimulation/WingStudy.SLDASM
254.1 x 43.8 x 894.6 mm
Ailerons x 4
AileronsRib250mm x 4
Rib250mm x 3
stick x 4
Stick2 x 4
aileronStick
XPSEnclosure
spar
mainspar

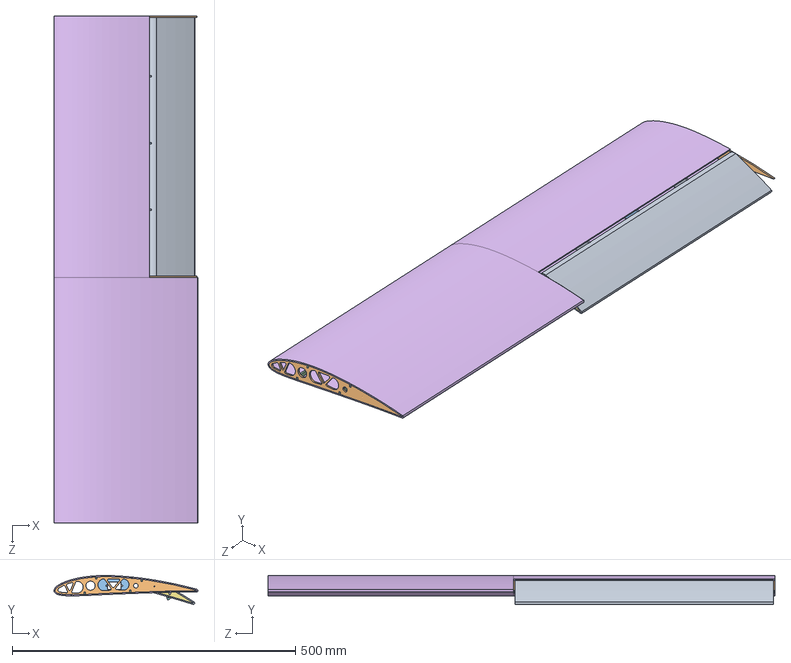
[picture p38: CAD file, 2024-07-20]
Manufacturing/ДетальнаяМодель/Модель/Крыло/ОблегченноеКрыло/LightWingRight.SLDASM
254.1 x 51.3 x 894.6 mm
LightAileronRib250mm x 2
LightRib250mm x 5
LightServoRibWithConnector250mm
stick x 4
Stick2 x 4
XPSEnclosure
Ailerons x 4
AileronsServo
AileronsXPSEnclosure

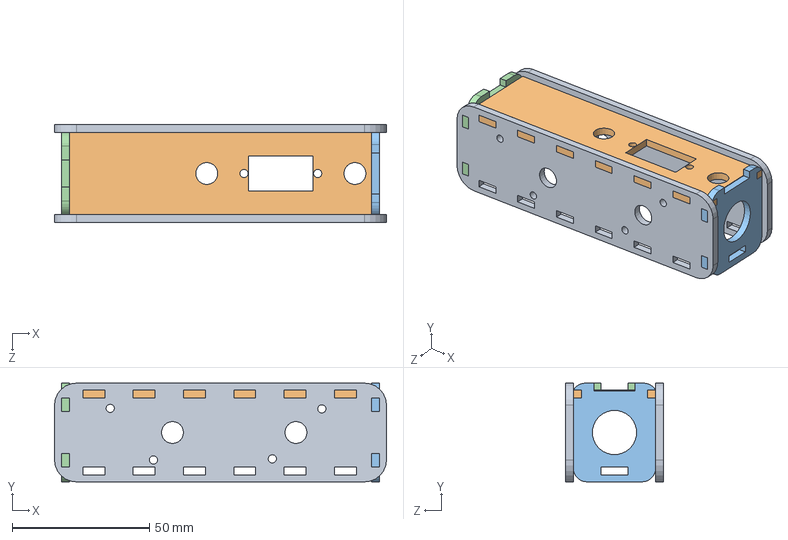
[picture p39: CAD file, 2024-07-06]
Manufacturing/ДетальнаяМодель/Модель/ХвостовоеОперение/КонекторХвоста/TailConectorAssembly.SLDASM
121.0 x 36.0 x 35.6 mm
TailConnector x 2
TailConnectorCup
TailConnectorFrontSecond
TailConnectorFront

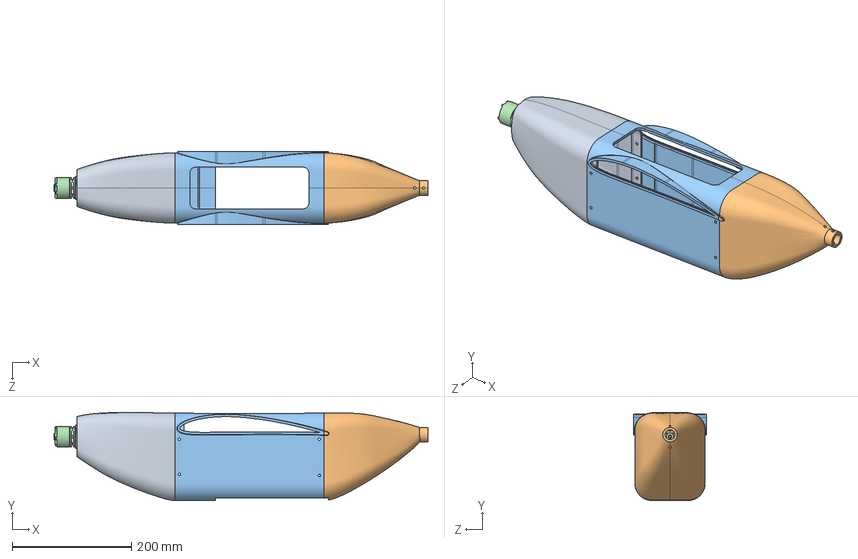
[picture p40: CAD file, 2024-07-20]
Manufacturing/ДетальнаяМодель/Модель/ТекущаяСборка/СборкаНовая.SLDASM
628.0 x 148.1 x 123.0 mm
FusNose
FusTail
FusBody
Sunnysky_2814_BrushlessMotor
MotorMount

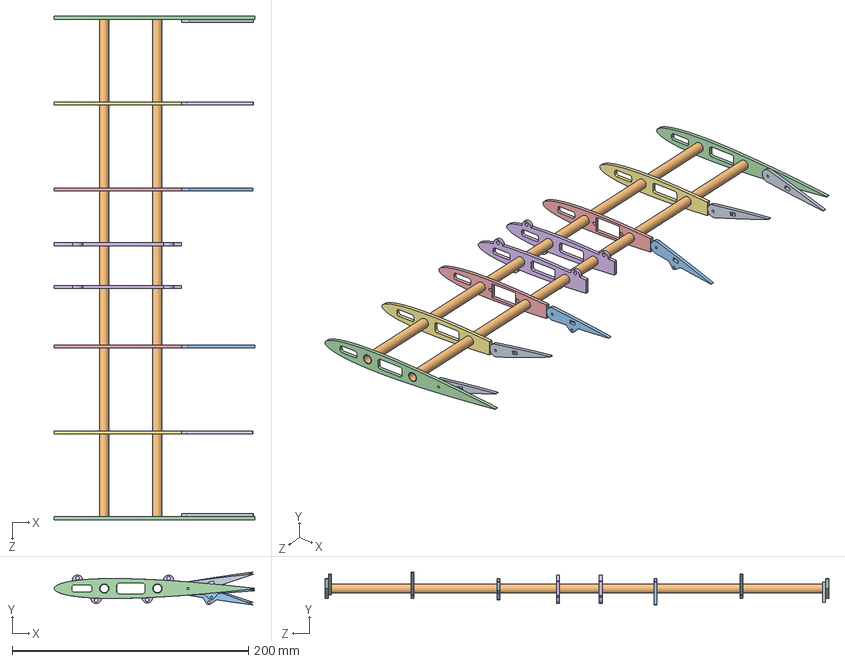
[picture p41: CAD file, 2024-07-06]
Manufacturing/ДетальнаяМодель/Модель/ХвостовоеОперение/ГоризонтальноеОперение/HorizontalTail.SLDASM
170.1 x 27.8 x 427.0 mm
Aileron170mmNACA0010 x 4
D8mm x 2
ServoAileron170mmNACA0010 x 2
Rib170mmNACA0010 x 2
ServoAileronRib170mmNACA0010 x 2
AileronRootRib170mmNACA0010 x 2
AileronRib170mmNACA0010 x 2

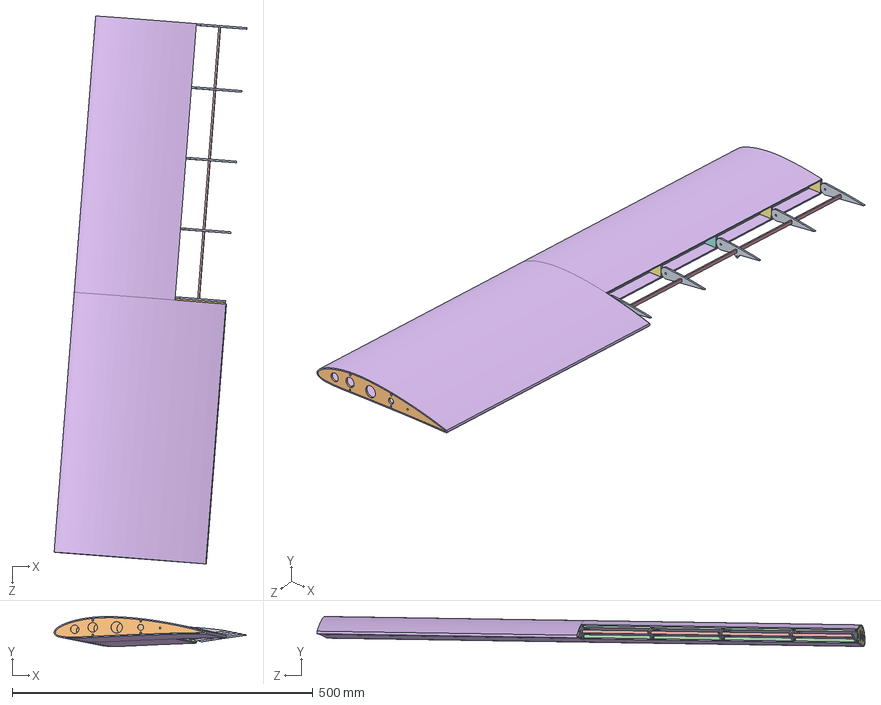
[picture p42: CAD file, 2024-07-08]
Manufacturing/ДетальнаяМодель/Модель/ТекущаяСборка/Wing.SLDASM
320.8 x 50.0 x 911.5 mm
Ailerons x 4
Rib250mm x 4
stick x 4
Stick2 x 4
aileronStick
XPSEnclosure
AileronsRib250mm x 3
AileronsRib250mmServo
AileronsServo

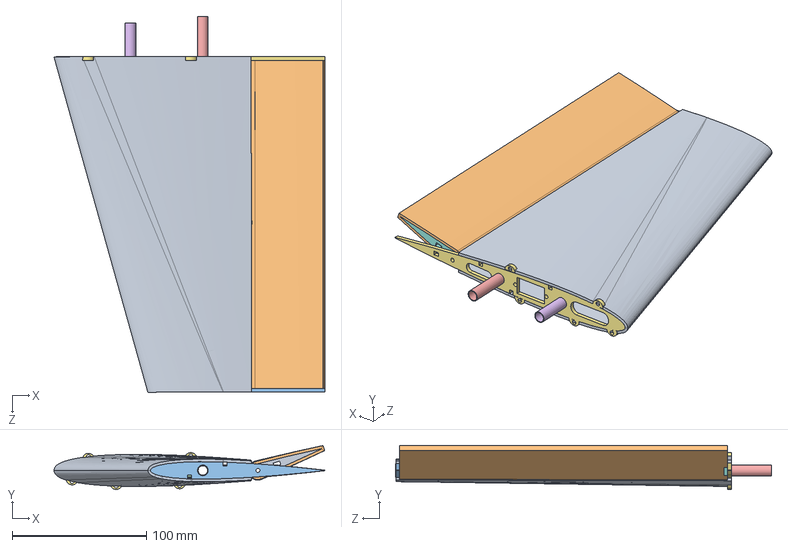
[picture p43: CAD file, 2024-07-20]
Manufacturing/ДетальнаяМодель/Модель/ХвостовоеОперение/Киль/VerticalTail.SLDASM
201.9 x 32.8 x 280.5 mm
RudderFin130mm
RudderFin166mm
nerv_fin_130
nerv_fin_166.4
MainSparVerticalTail
AdditionalSparVerticalTail
ServoRib_fin_200
RudderServo
VerticalTailXPSEnclosure
RudderXPSEnclosure

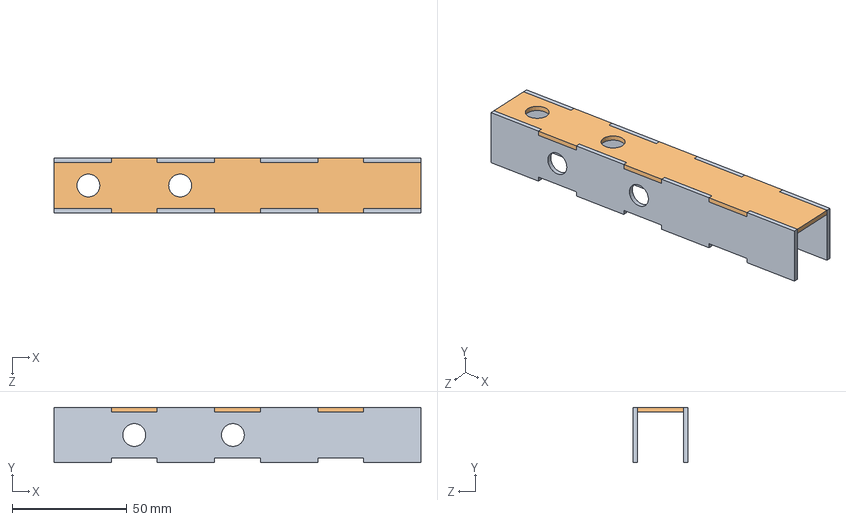
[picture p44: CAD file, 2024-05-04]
PreliminaryDesign/DetailedModel/Коробка хвост.SLDASM
160.0 x 24.0 x 24.0 mm
Хвост боковая пластина x 2
хвост верхняя пластна

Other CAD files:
Manufacturing/ДетальнаяМодель/Модель/Крыло/Wing.SLDASM
Manufacturing/ДетальнаяМодель/Модель/ТекущаяСборка/TailConectorAssembly.SLDASM
PreliminaryDesign/DetailedModel/Wing/Крылья.SLDASM
Manufacturing/ДетальнаяМодель/Модель/Крыло/WingLeft.SLDASM
ConceptualDesign/model/cargo.SLDPRT
ConceptualDesign/model/pixhawk.STEP
ConceptualDesign/model/refeeree_box_down.SLDPRT
ConceptualDesign/model/wing.SLDPRT
Manufacturing/3DPrintedAssembly/Aileron.SLDPRT
Manufacturing/3DPrintedAssembly/AileronLeft.SLDPRT
Manufacturing/3DPrintedAssembly/BatteryHolder.SLDPRT
Manufacturing/3DPrintedAssembly/BatteryHolder2.SLDPRT
Manufacturing/3DPrintedAssembly/Camera.SLDPRT
Manufacturing/3DPrintedAssembly/CarbonTube6x4x500mm.SLDPRT
Manufacturing/3DPrintedAssembly/CarbonTube8x6x1000mm.SLDPRT
Manufacturing/3DPrintedAssembly/Cargo2.SLDPRT
Manufacturing/3DPrintedAssembly/ESC60A.SLDPRT
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

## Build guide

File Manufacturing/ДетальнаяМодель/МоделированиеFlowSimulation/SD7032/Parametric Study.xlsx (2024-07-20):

 | Design Point 1 | Design Point 2 | Design Point 3 | Design Point 4 | Design Point 5
Angle of attack (Initial and Ambient Conditions) [°] | -1 | 0 | 1 | 2 | 3
GG Average Velocity 1 [m/s] | 17.99461803 | 18.0039185 | 18.03030752 | 18.03546702 | 18.03913142
GG Force (X) 2 [N] | 1.821171319 | 1.376724186 | 1.287484965 | 0.8716706713 | 0.7110303687
GG Force (Y) 3 [N] | 9.786775447 | 12.36928536 | 17.80167306 | 20.98416888 | 24.59933931
GG Force (Z) 4 [N] | 2.609782687 | 2.498299366 | 2.164325533 | 2.036552659 | 1.962297697
GG Torque (X) 5 [N*m] | -4.497046578 | -5.560795424 | -7.74490033 | -9.019721797 | -10.56994637
GG Torque (Y) 6 [N*m] | -0.4919074306 | -0.6530177489 | -0.6663639596 | -0.7932169036 | -0.8844889809
GG Torque (Z) 7 [N*m] | 1.182966772 | 1.543731326 | 2.290830201 | 2.638001758 | 3.014716237
F | M |  | FxM | F*F | r1 | t | r2
2.574969929 | 0 |  | 163.1224411 | 1274.228725 | 0.1280166095 | 0.001 | 0.2911390506
35.60334612 | 0 |  | -11.79763776 |  | -0.009258649981 |  | -0.02105628775
0 | 4.581660403 |  | 0 |  | 0 |  | 0

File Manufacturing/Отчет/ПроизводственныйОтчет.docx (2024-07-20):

Производственный отчет команды «ФАКИшники»

# 1. Сокращения и обозначения

l - размах | λ - удлинение | η – сужение крыла | b –ср. аэрод. хорда

# 2. Основные изменения конструкции ЛА

### 2.1 Фюзеляж

Вид фюзеляжа не претерпел существенных изменений, оставшись вытянутым в продольном направлении телом, поперечным сечением которого является прямоугольник со скругленными углами. Размер преимущественно определялся габаритами груза, так длина фюзеляжа (без учета хвостовой балки) составила 0.6 м , эквивалентный диаметр - 0.14 м , В верхней и нижней частях расположены вырезы для доступа с БРЭО и сброса груза соответственно (Рис.1)

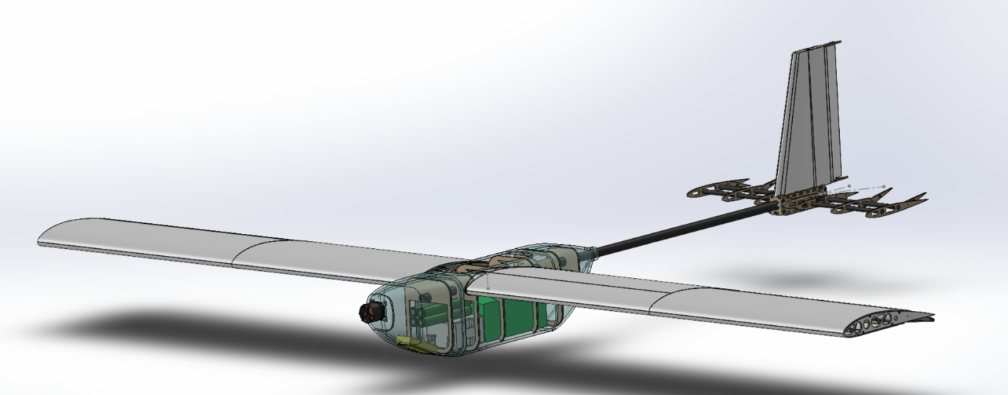
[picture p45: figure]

Рисунок 1. Общий вид ЛА

### 2.2 Геометрия крыла

Геометрические характеристики крыла были уточнены и приведены в соответствие с выбранной крейсерской скоростью ЛА - 18 м/с . Крыло было уменьшено, однако осталось прямоугольной формы. Геометрия крыла приведена в таблице 1 ниже.

Таблица 1. Геометрические характеристики крыла

| l, м | b, м | λ | η | S, м^2
Новое значение | 1.85 | 0.22 | 8.40 | 1.00 | 0.41
Предыдущее значение | 2.50 | 0.35 | 7.14 | 1.00 | 0.88

### 2.3 Хвостовое оперение

В силу изменения площади крыла последовало изменение площадей аэродинамических поверхностей хвостового оперения. Вновь, как и в промежуточном отчете, воспользуемся методом объемных коэффициентов, описанным в [1] и определим новые площади киля и горизонтального оперения; изменения в геометрии хвостового оперения приведены в таблице 2. Если в промежуточном отчете были выбраны значения объемных коэффициентов C_в =0.04 и C_г =0.5 , то сейчас их значения составили 0.045 и 0.6 соответственно для увеличения путевой и продольной стабильности ЛА, что будет обсуждено позже.

Таблица 2. Геометрические характеристики хвостового оперения

| l, м | b, м | λ | η | S, м^2
Киль | 0.24 | 0.16 | 1.50 | 0.60 | 0.04
Горизонтальное оперение | 0.53 | 0.12 | 4.42 | 1.00 | 0.06

### 2.4 Силовая установка

Проведя расчеты для новых геометрических характеристик ЛА, команда приняла решение о целесообразности замены мотора на иной, менее мощный, но удовлетворяющий требованиям к тяге в крейсерском режиме полета и во время набора высоты. Таковым мотором стал Sunnysky X2814, характеристики которого представлены в таблице 3 ниже. Объемы аккумуляторных батарей и их тип изменений не претерпели. Предлагается использовать литий-ионные батареи Molicel 18650 емкостью 2.8 А∙ч в сборке 4S2P

Таблица 3. Характеристики силовой установки

Масса, кг | Максимальная мощность, Вт | Максимальный потребляемый ток, А | Воздушный винт
0.13 | 680 | 50 | 11x6

# 3. Аэродинамические расчеты

Основным инструментом в определении сил, моментов сил и их характера воздействия на ЛА являлись прикладные инженерные пакеты вычислительной гидродинамики. Уточнение геометрии аэродинамических поверхностей в большей мере основывалось на результатах численного моделирования, произведенного в этих программах. Командой был проведен анализ сил, моментов сил, определены им соответствующие аэродинамические коэффициенты в зависимости от угла атаки. Также была изучена продольная и динамическая устойчивость ЛА.

#### 3.1 Выбор аэродинамических профилей

В силу изменений геометрических размеров ЛА последовало изменение эксплуатационных чисел Рейнольдса, что сказалось на выборе профилей крыла и хвостового оперения. Сейчас эксплуатационный диапазон чисел Рейнольдса составил 240 000 – 260 000. Это обстоятельство предполагает использование малоскоростных профилей, которые подробно описаны в источнике [2]. Так для крыла был выбран профиль SD7032, специально разработанный для эксплуатации на низких скоростях до 300 000 Re. Для хвостового оперения был выбран симметричный NACA0009.

#### 3.2 Аэродинамические коэффициенты сил и моментов сил

Для определения аэродинамических коэффициентов было произведено параметрическое исследование полета ЛА с крейсерской скоростью 18 м/с , в качестве параметра выступал угол атаки α (угол между продольной осью ЛА и вектором скорости, набегающего потока). Анализ был произведен для полета с грузом. В течение расчета для каждого из углов атаки определялись силы и моменты сил, действующих на ЛА, по ним пересчитывались аэродинамические коэффициенты. Для исключения существенных ошибок численного расчета, связанных с типом сетки и ее шагом по пространству (разным сеткам на одной и той же модели может соответствовать разные результаты моделирования, что нужно исключить), была использована адаптивная сетка (Рис. 2). Только после того, как очередной раз расчетная область была разбита на более мелкие ячейки и зафиксировано, что сходимость измеряемых величин не претерпевает существенного изменения, исследование останавливалось, а результат признавался, как не зависящий от сетки (ее мелкости разбиения).

Результаты исследования приведены ниже в таблице 4

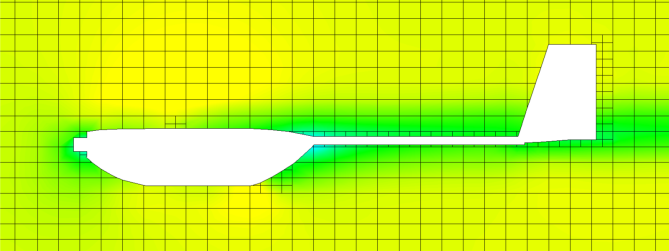
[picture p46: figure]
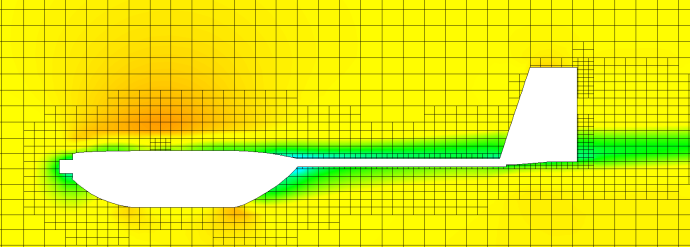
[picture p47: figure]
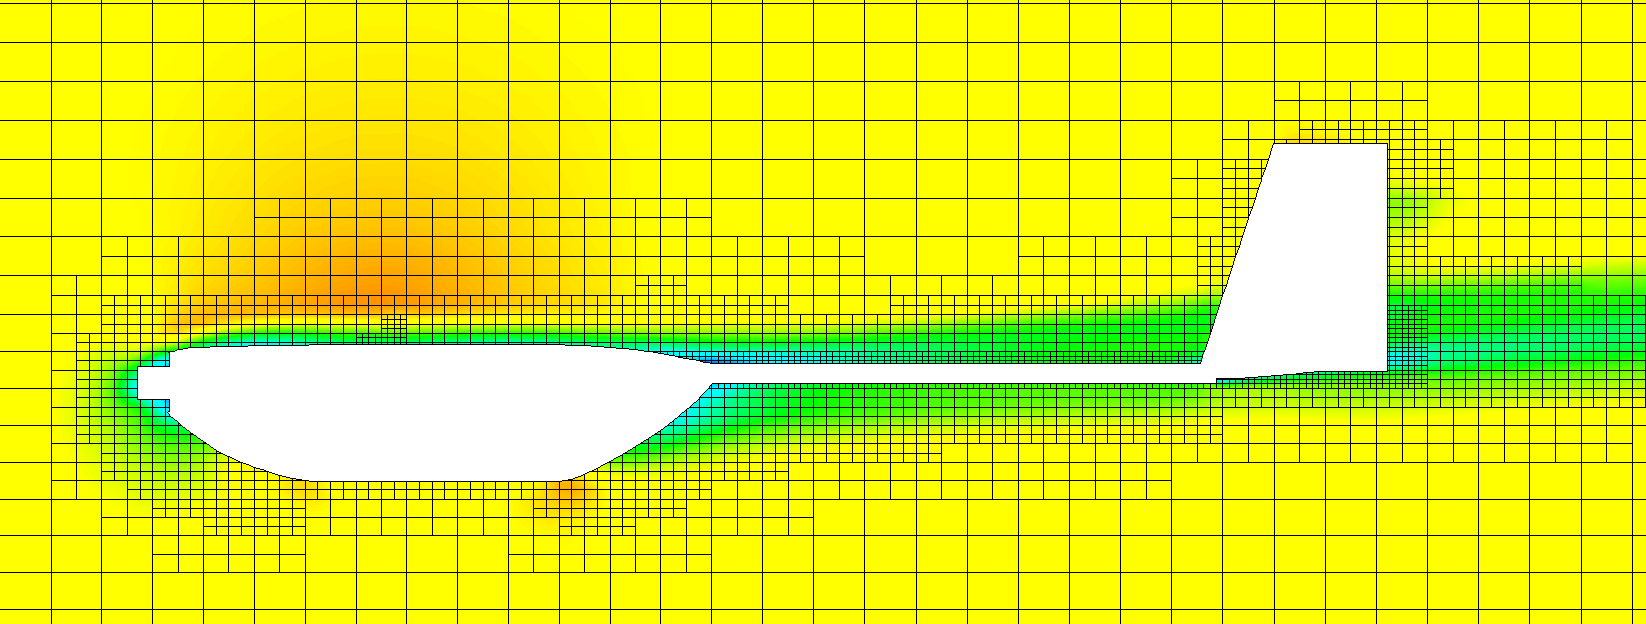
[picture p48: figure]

Рисунок 2.Уровни измельчения адаптивной сетки

Таблица 4. Результаты моделирования сил и моментов, действующих на ЛА

| -4° | -3° | - 2° | -1° | 0° | 1° | 2° | 3° | 4°
F_x | -4.02 | -3.83 | -3.09 | -3.53 | -3.18 | -2.81 | -1.33 | -1.64 | 0.63
F_y | 5.54 | 12.39 | 18.22 | 25.96 | 29.65 | 37.31 | 42.50 | 48.30 | 54.04
F_z | -0.08 | 0.07 | -0.08 | 0.04 | 0.271 | 0.031 | 0.009 | 0.045 | 0.04
M_x | -0.01 | 0.01 | -0.01 | 0.03 | 0.08 | -0.01 | -0.02 | -0.02 | 0.00
M_y | -0.01 | 0.05 | 0.01 | 0.05 | 0.04 | 0.00 | 0.05 | 0.02 | 0.07
M_z | 2.30 | 2.32 | 1.89 | 2.27 | 2.35 | 2.16 | 1.59 | 2.38 | 2.73
| 5° | 6° | 7 ° | 8° | 9° | 10° | 11° | 12° | 13°
F_x | -1.49 | 1.35 | 2.31 | 3.03 | 3.84 | 3.92 | 1.57 | 4.00 | 1.56
F_y | 57.20 | 68.40 | 72.49 | 75.75 | 79.39 | 81.73 | 75.47 | 80.83 | 78.61
F_z | 0.02 | 0.04 | 0.02 | 0.12 | 0.01 | 0.10 | -0.05 | 0.14 | 0.12
M_x | 0.00 | 0.00 | -0.06 | 0.03 | -0.04 | 0.04 | 0.05 | 0.07 | 0.10
M_y | 0.03 | 0.04 | 0.04 | 0.07 | 0.03 | 0.00 | -0.03 | 0.05 | 0.02
M_z | 2.51 | 2.21 | 1.81 | 1.57 | 0.90 | 0.84 | -0.78 | 0.18 | 0.11

Приведем зависимости аэродинамических коэффициентов от угла атаки (Рис. 3), пересчитав значения сил и моментов сил из таблицы выше, используя значение скоростного напора q=198 Па и геометрических характеристик крыла.

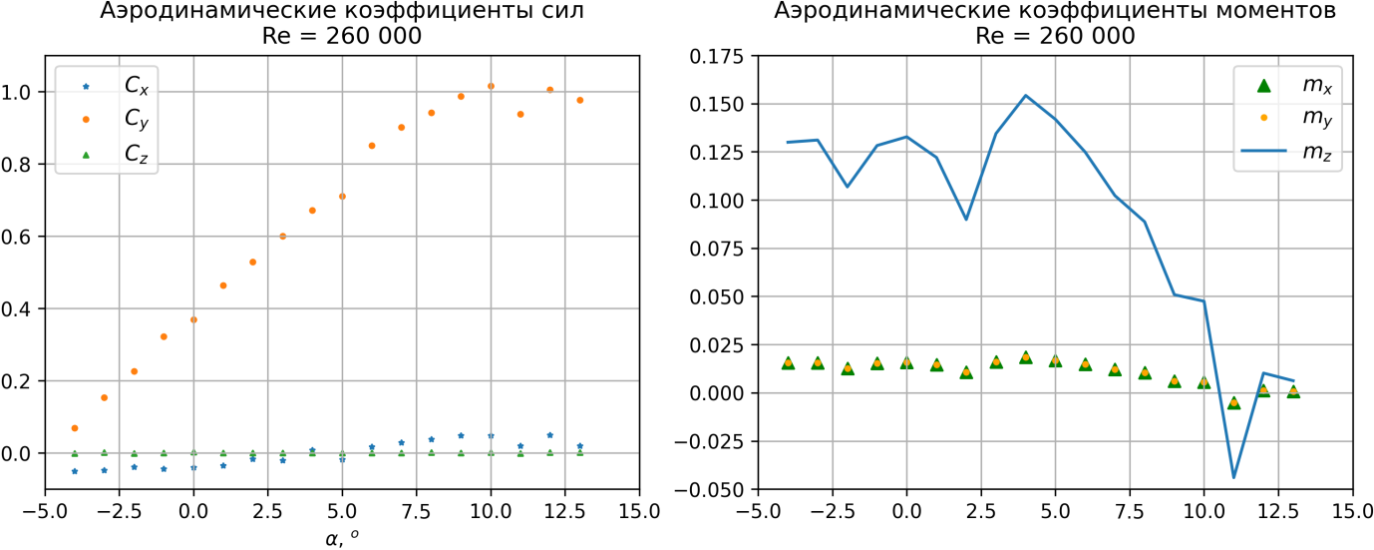
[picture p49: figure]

Рисунок 3. Аэродинамические коэффициенты сил и моментов

#### 3.3 Аэродинамическое качество

Определим аэродинамическое качество ЛА, как отношение подъемной силы к силам сопротивления, пересчитав значения сил из таблицы 4, мы получим вышеупомянутое отношение (Рис. 4)

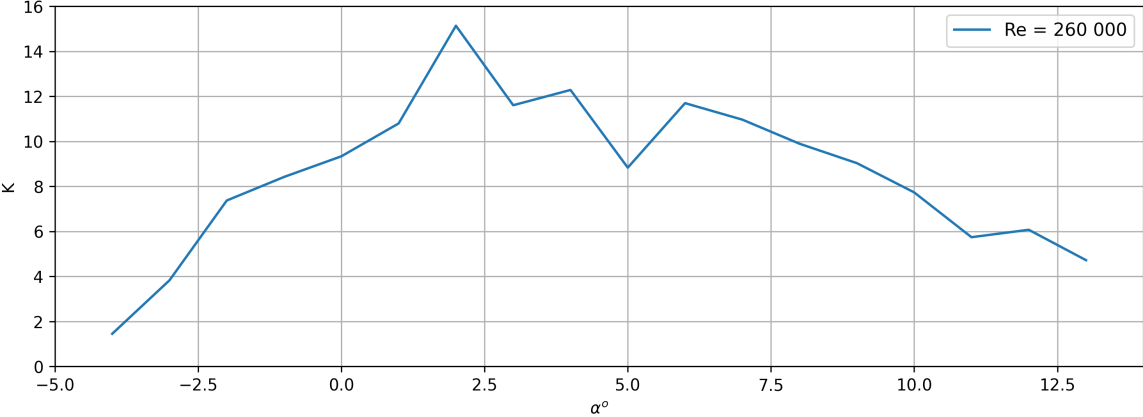
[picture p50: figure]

Рисунок 4.Зависимость аэродинамического качества ЛА от угла атаки

#### 3.4 Динамические производные коэффициентов моментов сил

Для динамической стабильности ЛА необходимо, чтобы производные аэродинамических коэффициентов моментов по соответствующим угловым скоростям ЛА в проекции на оси связной системы координат были отрицательны (1). Оценка этих динамических производных также производилась с помощью численного моделирования. С ЛА связывалась неинерциальная система координат с началом в центре масс.

| (∂m_i)/(∂ω_i)<0, ∀ i∈{x, y,z} | (1)

В пространстве задавалась неподвижная система координат, относительно которой происходило вращение расчетной области и модели (неподвижная система координат необязательно должна находиться в расчетной области). В неинерциальной системе координат, связанной с ЛА, измерялись силы и моменты сил (с учетом сил инерции), по которым вычислялись аэродинамические коэффициенты. Динамические производные находились как отношение разности коэффициента момента сил при вращении и коэффициента момента в крейсерском полете без вращения m_(i0) к угловой скорости вращения (2). В таблице 5 представлены результаты измерений, в том числе перекрёстных динамических производных.

| (∂m_i)/(∂ω_i)= (m_i -m_(i0))/(ω_i) | (2)

Таблица 5. Матрица динамических производных

| m_x | m_y | m_z
ω_x | -0.08 с/(рад) | -0.03 с/(рад) | 2.5 с/(рад)
ω_y | -0.01 с/(рад) | -0.01 с/(рад) | 0.12 с/(рад)
ω_z | 0.00 с/(рад) | 0.00 с/(рад) | -6.50 с/(рад)

#### 3.5 Балансировочная кривая

Для выбранного отклонения руля высоты δ_в произведем анализ ЛА и определим угол атаки, при котором m_z =0 , набор пар (α, δ_в ) определит балансировочную кривую (Рис. 5)

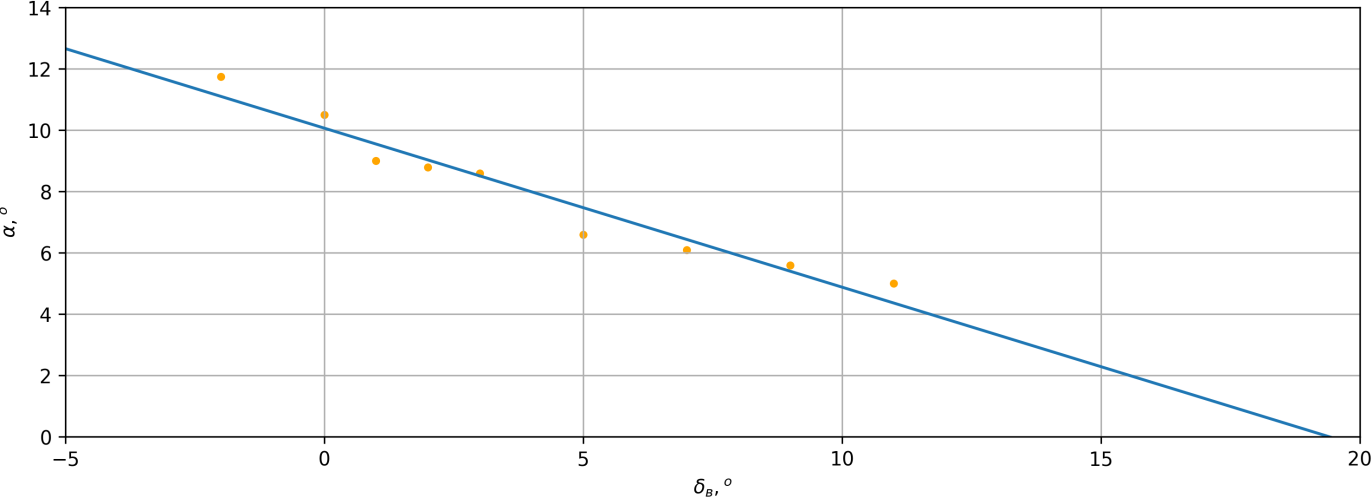
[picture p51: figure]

Рисунок 5. Балансировочная кривая

#### 3.6 Устойчивость в продольном канале

Устойчивость ЛА в продольном канале по перегрузке можем оценить по характеру зависимости m_z (C_y ) , для статической устойчивости необходимо, чтобы было выполнено выражение вида ((m_z )_α)/((C_y )_α)<0 , а величину равную полной производной коэффициента момента тангажа по коэффициенту подъемной силы с обратным знаком назовем запасом устойчивости по перегрузке в продольном канале σ_n при некотором фиксированном положении руля высоты. Рассмотри рисунок 3 и найдем запас устойчивости в точке, где m_z = 0, получим

| σ_n = - ((m_z )_α)/((C_y )_α)= 0.021/0.064=0.32 | (3)

# 4. Прочностные расчеты

  4.1 Материалы конструкции

В качестве основного материалы был выбран полиэтилентерефталат-гликоль – PETG пластик – за свою устойчивость к относительно высоким температурам и механическим характеристикам. Фюзеляж, хвостовое оперение планируется изготовить из PETG.

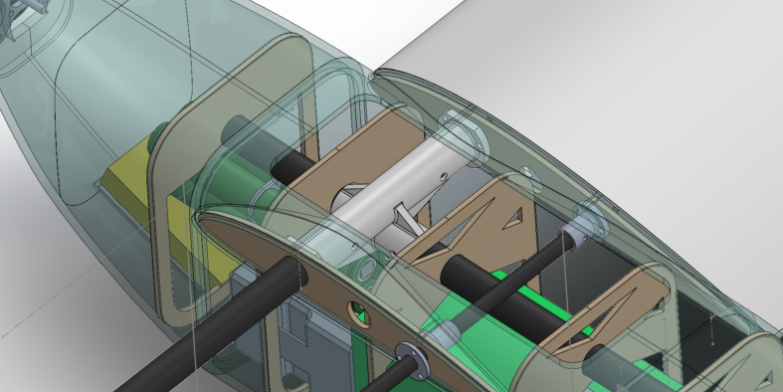
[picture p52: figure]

Фанера – основной материал шпангоутов фюзеляжа. Хорошие механические характеристики PETG пластика сказываются на его плотности, потому для облегчения конструкции фюзеляж будет представлять тонкостенную конструкцию с толщиной стенок не более 2 слоев пластика, укладываемого принтером. Фанерные шпангоуты призваны увеличить прочность конструкции фюзеляжа и придать жесткость (Рис. 6)

Рисунок 6 Фанерные шпангоуты фюзеляжа

Углеволокно – материал пултрузионных трубок, используемых в качестве лонжеронов крыла.

Ниже в таблице 6 приведены основные механические характеристики, используемых материалов на основе источников [3 - 4].

Таблица 6. Характеристики материалов

| PETG | Углеволокно (пултрузионное) | Фанера (из лиственницы) | Стекловолокно (в эпоксидной матрице)
Модуль Юнга | 2.1 ГПа | 40 ГПа (вдоль волокон) 10 ГПа (поперек волокон) | 7.7 ГПа | 25 ГПа
Предел прочности на сжатие | 28 МПа | 100 МПа | 35 МПа | 430 МПа
Предел прочности на растяжение | 28 МПа | 400 МПа (вдоль волокон) 18 МПА (поперек волокон) | 30 МПа | 430 МПа
Коэффициент Пуассона | 0.4 | 0.1 | 0.07 | 0.2
Модуль сдвига | 1.1 ГПа | 5 ГПа | 150 МПа | 4 ГПа
Плотность, (кг)/(м^3) | 1270 | 1600 | 700 | 1900

  4.2 Эпюры поперечных сил и изгибающих моментов

Расчет эпюр поперечных сил, изгибающих моментов и деформации основан на полученном из численного моделирования распределении аэродинамических сил вдоль размаха ЛА, представленном на рисунке 7

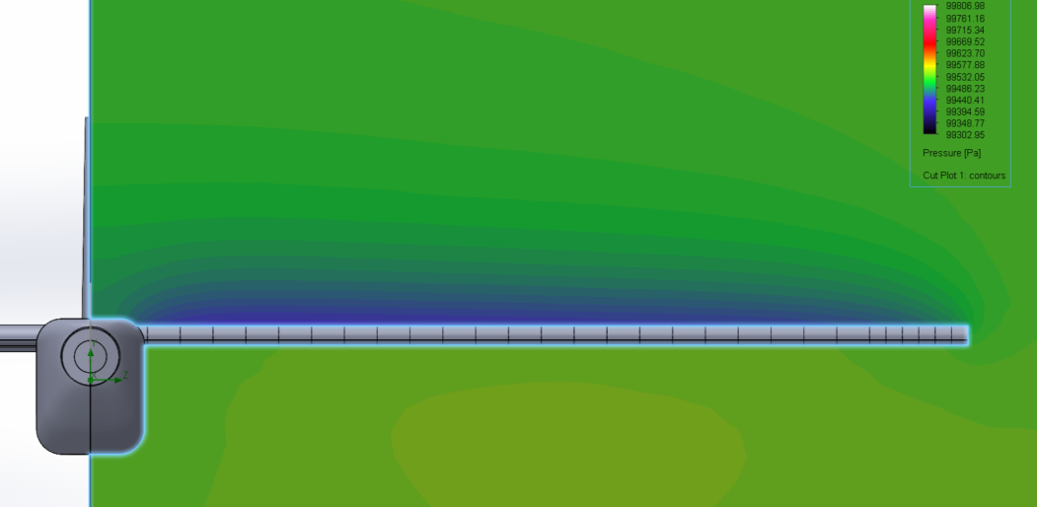
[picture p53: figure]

Рисунок 7. Распределение давления вдоль консоли крыла

Крыло было представлено, как балка с шарнирным закреплением на конце, на которую действует распределённая аэродинамическая нагрузка, полученная из численного моделирования и вес собственных элементов конструкции. Поперечная сила Q(x) , действующая на крыло считались, как сумма всех распределенных нагрузок действующих на крыло:

| Q(x)= ∫_l^x q(z)dz | (4)

где q(x) – распределённая нагрузка на крыло вдоль размаха

Моменты сил были подсчитаны следующим образом:

| M(x)= ∫_l^x Q(z)dz | (5)

Линейное смещение крыла-балки было подсчитано путем повторного интегрирования моментов сил M(x) вдоль размаха по следующей формуле:

| y^('') (x)= (M(x))/(EI) | (6)

где E – модуль Юнга материала балки – углепластик, I – геометрический момент инерции сечения лонжерона крыла, y^('') - линейное вертикальное смещение лонжерона крыла. На рисунке ниже представлены эпюры изгибающих моментов, поперечных сил и эпюра деформации для горизонтального полета.

s

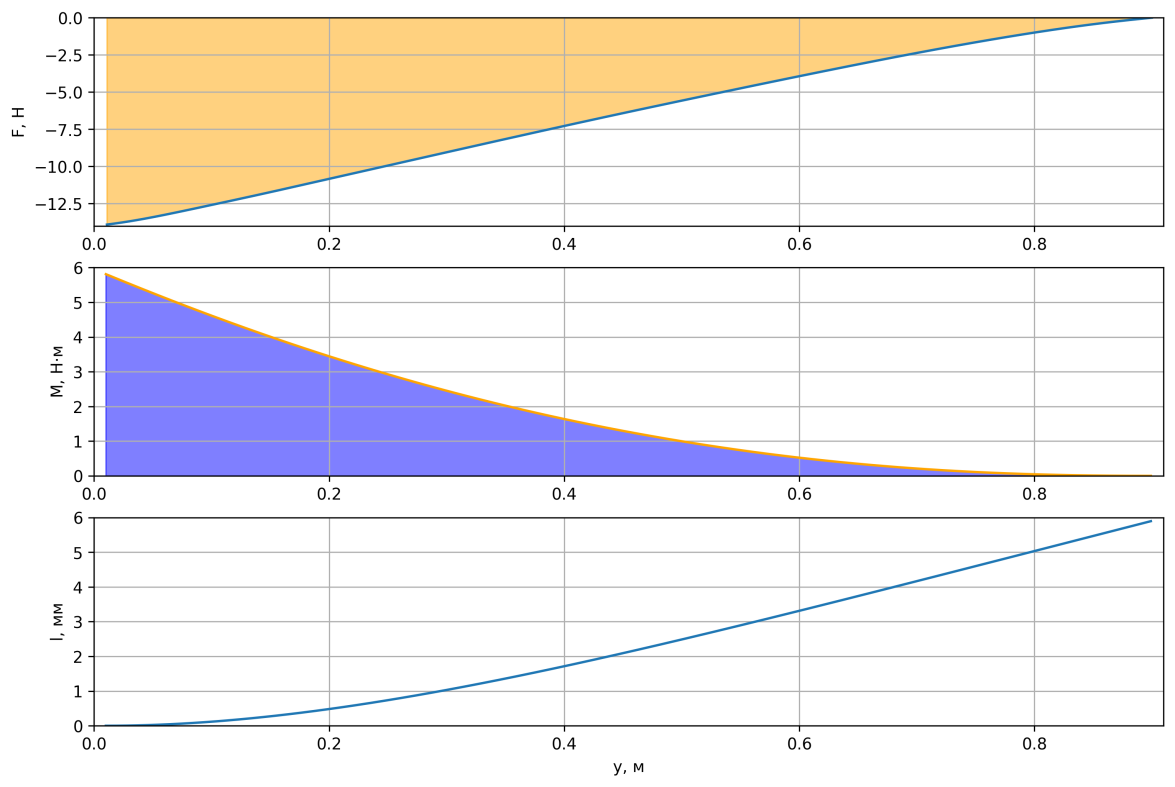
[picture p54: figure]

Рисунок 8 Эпюры поперечных сил, изгибающих моментов и деформации

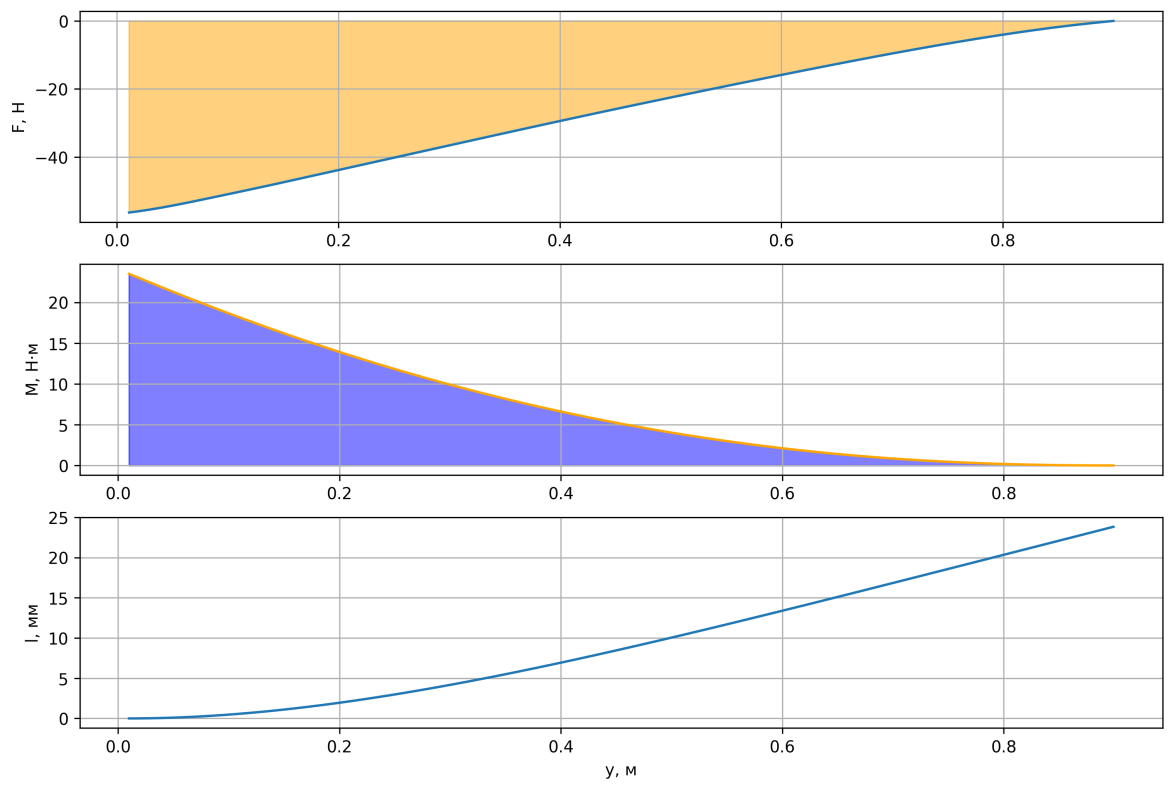
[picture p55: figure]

Рисунок 9. Эпюры поперечных сил, изгибающих моментов и деформации при перегрузке n = 4

  4.3 Наиболее нагруженные участки конструкции

Наиболее нагруженными участками конструкции являются моторама она же носовая часть фюзеляжа, места крепления крыла к хвостовой балки ЛА, на нее приходятся большая часть всех нагрузок испытываемых крылом при маневрах. Для исследования прочности элементов конструкции был проведен статический анализ в инженерных программных пакетах, результаты с указанием коэффициента безопасности представлены ниже на рисунках 10 и 11


Рисунок 10. Результаты моделирования четырехкратной перегрузки места крепления крыла

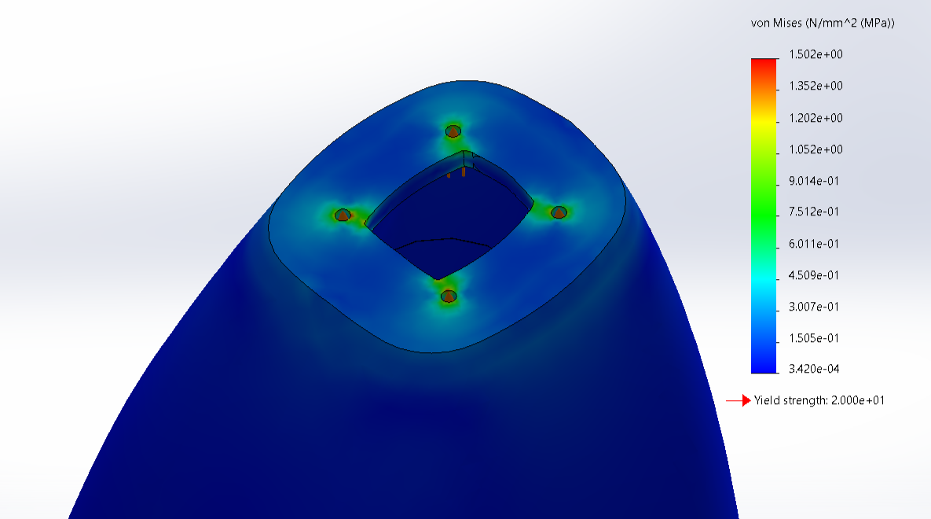
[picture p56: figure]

Рисунок 11 Результат моделирования приложенной тяги к мотораме. Распределение нагрузки.

Деталь, представленная на рисунке 10, служит для крепления лонжерона крыла и хвостовой балки ЛА, в процессе моделирования четырехкратной перегрузки была приложены сила в 250 Н, имитирующая действия лонжерона. Как видно из результатов моделирования, минимальный коэффициент безопасности не ниже 2. Материал детали – PETG.

# 5. Бортовое оборудование

Принцип устройства БРЭО по сравнению с промежуточным отчетом не претерпел существенных изменений. Весь набор бортового оборудования поделен на 2 систем: система управления полетом, система контроля доставки груза. Однако от системы компьютерного зрения пришлось отказаться – сложности и большие времени затраты при реализации.

  5.1 Блок-схема БРЭО

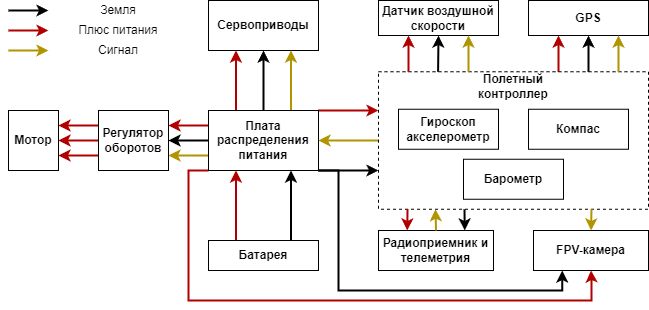
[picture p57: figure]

Рисунок 12. Блок-схема системы управления полетом

Блок-схема БРЭО представлена на рисунке 12 выше. Используется плата распределения питания, для снабжения сервоприводов, полетного контроллера и мотора соответствующим им напряжением. Подсистема полетного контроллера ответственна за обработку данных с датчиков непосредственно реализованных на печатной плате: гироскоп, акселерометр, барометр, компас; а так же выносных датчиков – GPS приемник, датчик скорости воздушного потока. Осуществляется обработка поступающего управляющего сигнала с радиоприемника. Также полетный контроллер ответственен за перераспределение управляющего сигнала на сервоприводы и мотор.

Система контроля доставки груза – микроконтроллерный блок, реализованный непосредственно на печатной плате полетного контроллера. В качестве управляемого устройства выступает сервопривод, обеспечивающий фиксацию груза в объеме фюзеляжа ЛА и его сброс в случае достижения целевой GPS координаты.

  5.2 Полетный конроллер и плата распределения питания

Как и планировалось в промежуточном отчете командой был разработан полетный контроллер и плата распределения питания для питания как контроллера, так и сервоприводов, требующих напряжения питания 8 вольт. Принципиальная схема полетного контроллера представлена на рисунке 14, а также дублирована на github репозитории команды, на который можно перейти по QR-коду на рисунке 15

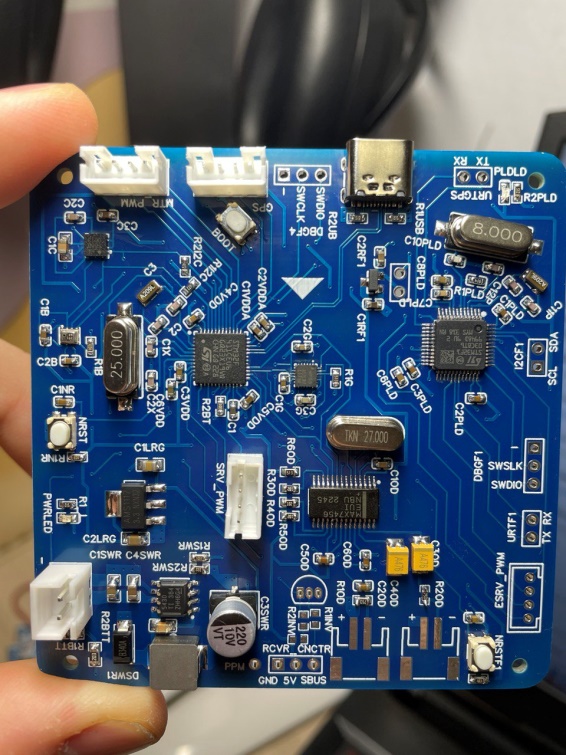
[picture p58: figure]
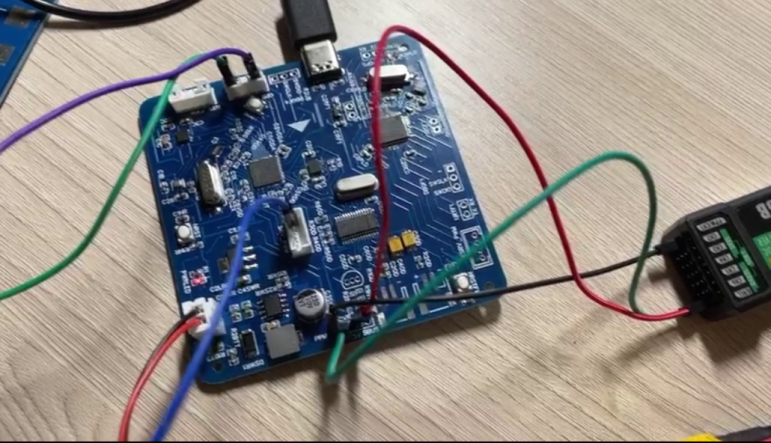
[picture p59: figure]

Рисунок 13. Плата полетного контроллера

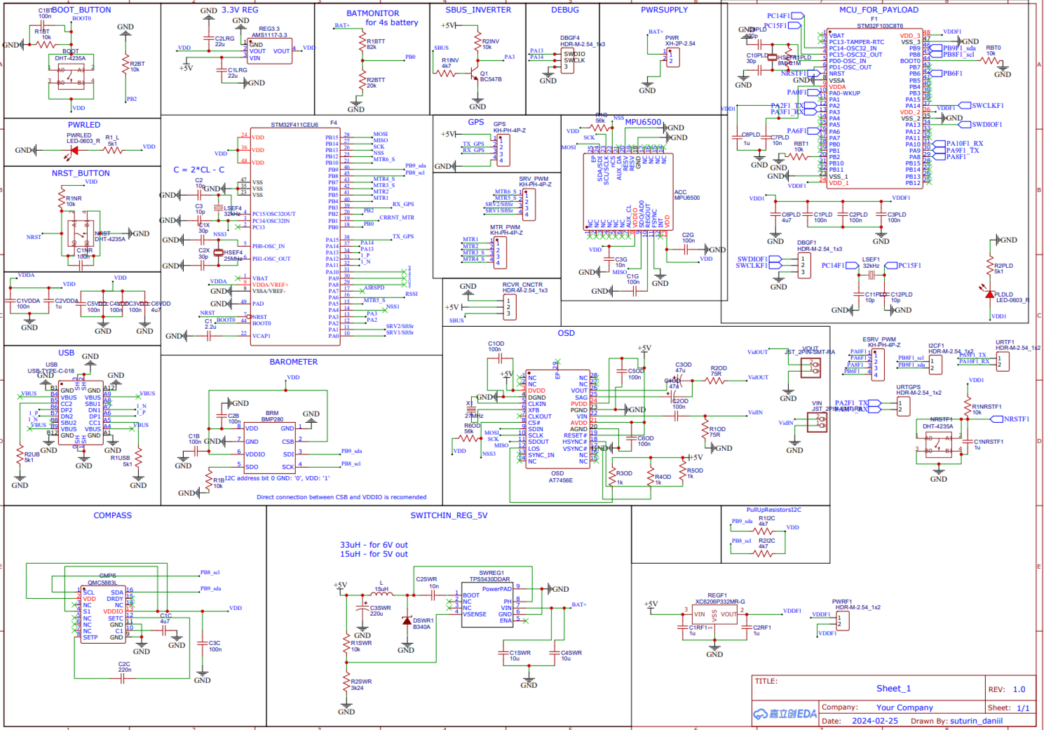
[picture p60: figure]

Рисунок 14. Схема полетного контроллера

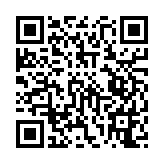
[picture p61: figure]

Рисунок 15. Ссылка на github репозиторий

  5.3 Расчет потребления БРЭО

С учетом известного аэродинамического качества пересчитаем максимальное время полета ЛА, результат представим на рисунке 16.

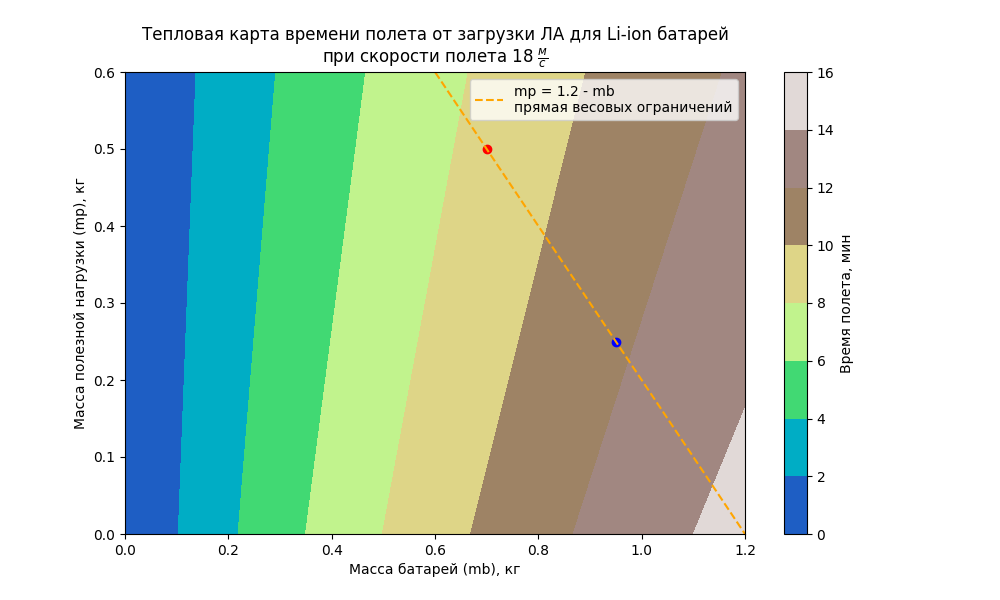
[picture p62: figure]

Рисунок 16. Время полета ЛА при разной загрузке

  5.4 Действия в случае аварийных ситуаций

Таблица 7. Действия в случае отказа датчиков

Датчик | Случай отказа | Действия | Увеличение отказоустойчивости | Степень критичности
MPU6500 | Отказ на земле - ПК не включится | Замена ПК | Покупка качественных компонентов для ПК | Критично
| Отказ в воздухе - отсутствие стабилизации, прерывание полетного задания | Управление в ручном режиме
QMC5883L | В версии INAV 7.1 осуществлена возможность автономной навигации без магнетометра на основе показаний гироскопа и акселрометра | Продолжение полетного задания | На плате ПК в месте расположения датчика убран медный слой и высокотоковые линии рис.№ | Средняя критичность
BMP280 | ПК имеет канал GPS с данными о координате, скорости и высоте полета | Продолжение полетного задания | ПК должен находиться в среде без активных течений воздуха | Не критично
M10Q-5883 | Прерывание полетного задания | Управление в ручном режиме | Вабрана модель компаса с наименьшим временем холодного старта для увеличения числа доступных для навигации спутников | Критично
ASPD-4525 | Отказ датчика в ветренную погоду влияет на точность автономной посадки и контроля сваливания | Продолжение полетного задания | Надежная фиксация датчика к элементам конструкции ЛА | Средняя критичность

# 6. Описание процесса производства ЛА

Как было упомянуто в разделе описания материалов, основным материалом является пластик PETG, он относительно остальных пластиков прочный и температуростоек. Фанера – основной материал шпангоутов и всего сборного крыла ЛА. Углепластик и стеклопластик используются для лонжеронов и хвостовой балки.

Основной инструмент – 3д принтер, с его помощью планируется печатать детали фюзеляжа. Лазерный резчик по дереву необходим для быстрого изготовления типовых деталей сборного крыла: нервюр, стрингеров.

Процесс сборки ЛА – соединение частей фюзеляжа в единую конструкцию эпоксидным составом и вклейка фанерных шпангоутов, сбор консолей крыла и системы хвостового оперения (она изготавливается методом 3д печати)

Смета приложена на github репозитории команды

# 7. Отставания от графика и новые задачи

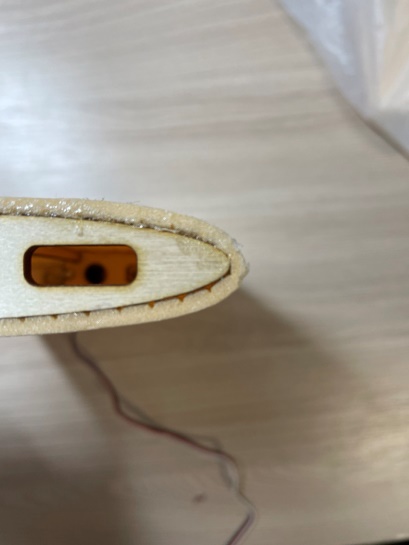
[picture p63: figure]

В процессе разработки ЛА возникли технологические проблемы, при обшивке крыла тонким слоем пенополистирола, профиль существенно меняется и утолщается (Рис. 17) Возможно, придется использовать термоусадочную пленку или изготавливать крылья методами 3д печати.

Рисунок 17. Профиль крыла

Полетный контроллер изготовлен, его функциональность проверена, управляющий сигнал принимается с пульта. Однако в процессе пайки платы был поврежден акселерометр, что привело к переориентации его осей, что не приемлемо для полетного контроллера. Поэтому сейчас стоит задача перепаять инерциальный модуль. Так же отстает от графика процесс разработки алгоритма сброса груза.

# 8. Используемая литература

[1] Raymer, D., Aircraft Design: A Conceptual Approach, American Institute of Aeronautics and Astronautics, Inc., 6th ed., 2018

[2] Christopher A. Lyon, Andy P. Broeren, Philippe Gigu`ere, Ashok Gopalarathnam, and Michael S. Selig: Summary of Low-Speed Airfoil Data. Volume 3

[3] https://www.performance-composites.com/carbonfibre/mechanicalproperties_2.asp Интернет ресурс

[4] Online materials information resource https://www.matweb.com/ Интернет ресурс

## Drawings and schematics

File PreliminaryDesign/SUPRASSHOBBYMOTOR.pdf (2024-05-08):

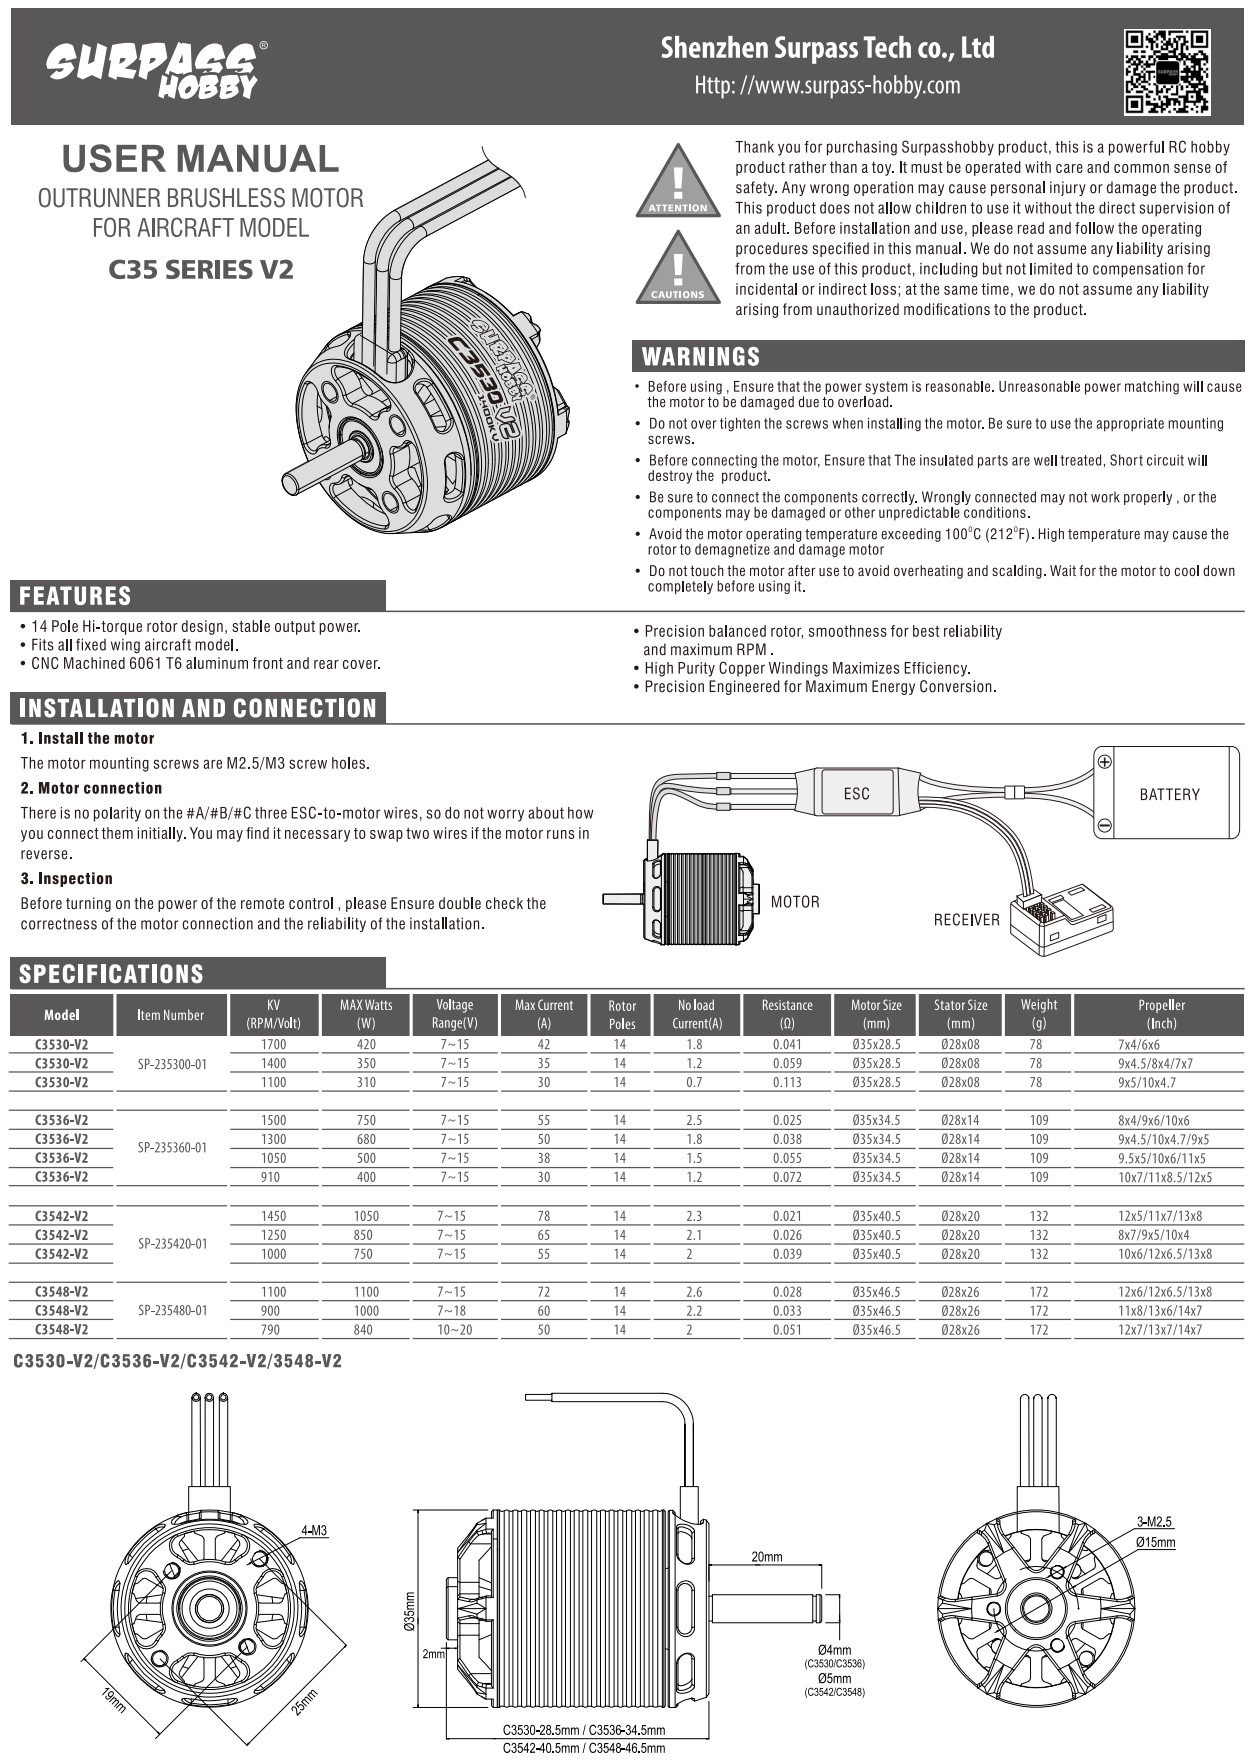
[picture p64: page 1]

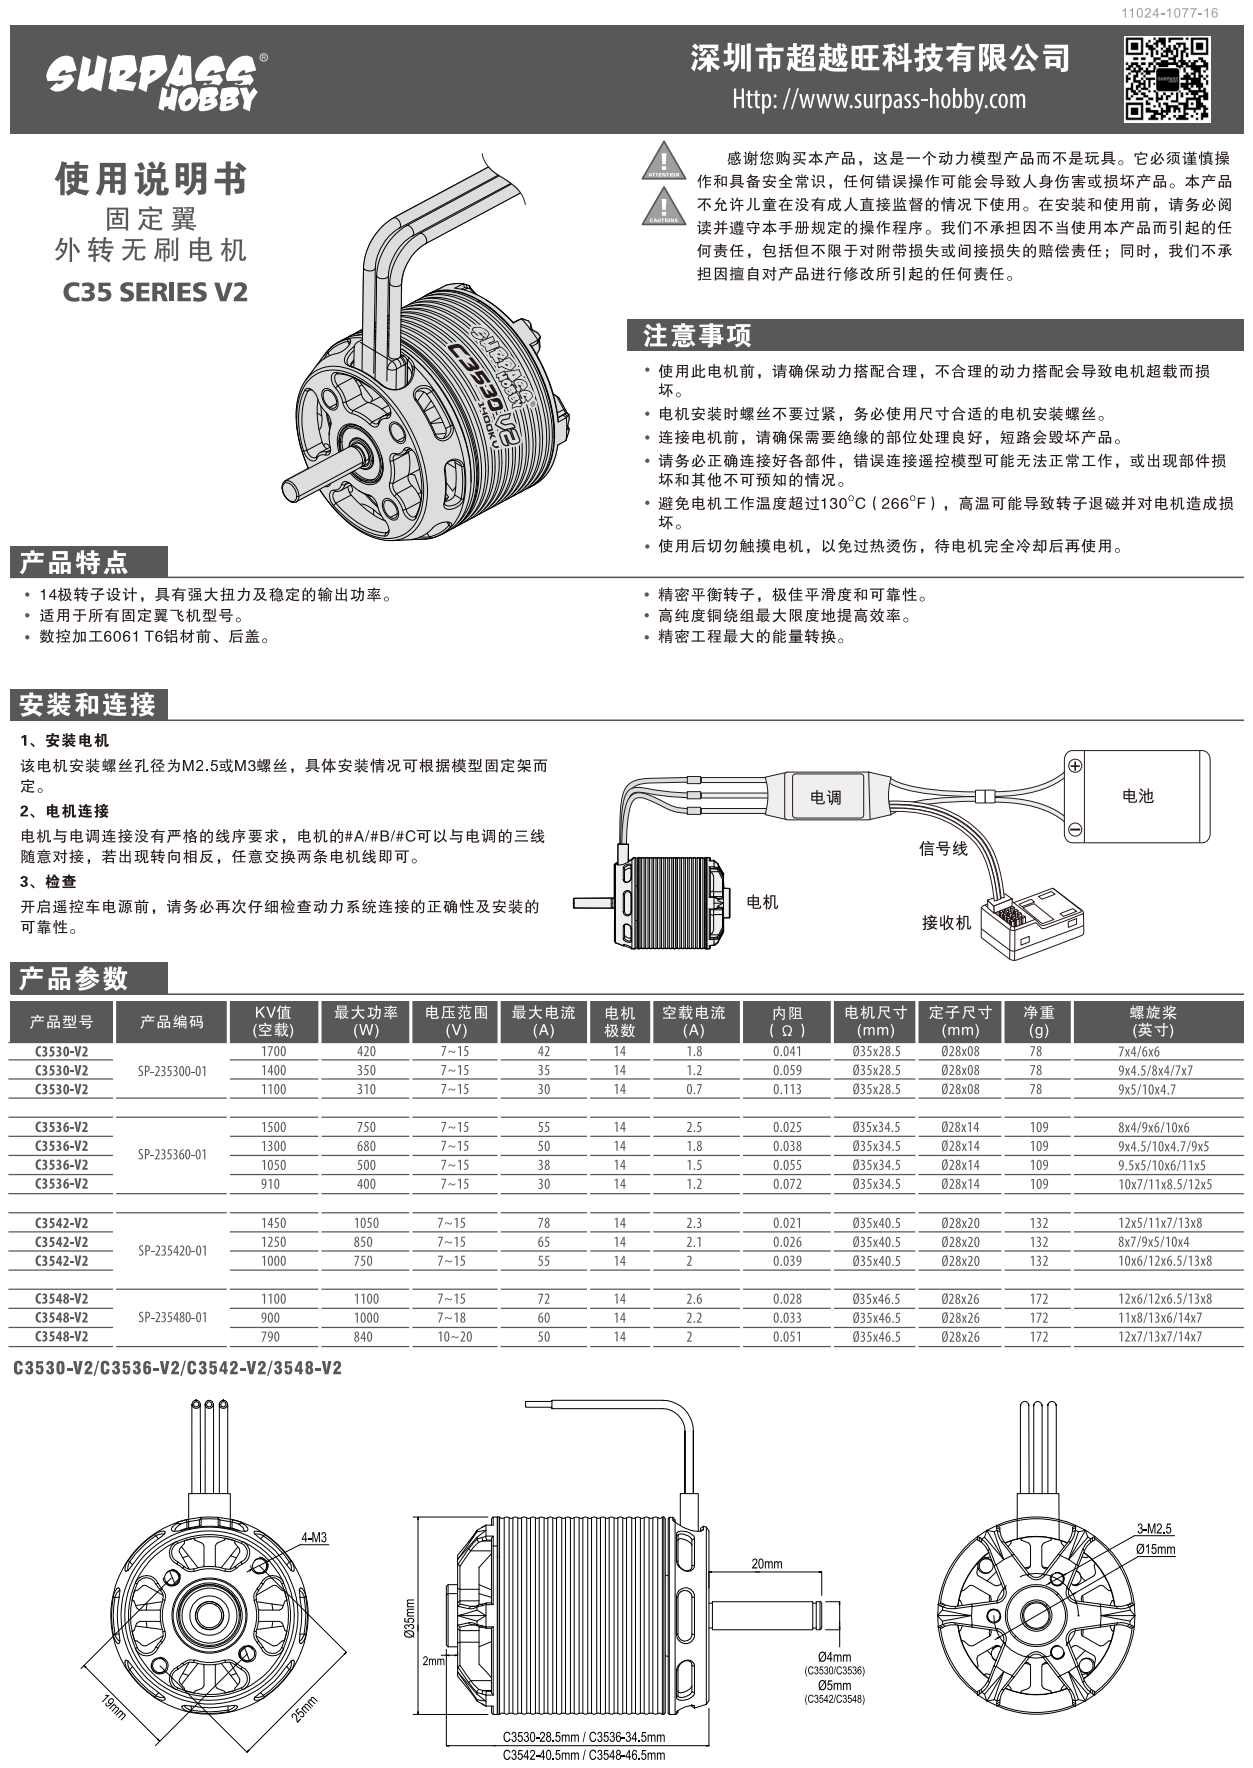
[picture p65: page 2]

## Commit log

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2024-04-05 Add files via upload
    Конечный вариант концепта
    [18650 Li-Ion.step, Propeller 10x5.5.STEP, cargo.SLDPRT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]
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2024-04-26 Упорядочил папки
    [18650 Li-Ion.step, Propeller 10x5.5.STEP, cargo.SLDPRT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]
2024-04-26 Добавил папку со сметой
    [Costings.xlsx]
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2024-04-26 Перенес концепт в папку
    [18650 Li-Ion.step, Propeller 10x5.5.STEP, cargo.SLDPRT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]
2024-05-01 Обновил gerber файлы
    [Suturin_FC_PCB.GBL, Suturin_FC_PCB.GBO, Suturin_FC_PCB.GBP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]
2024-05-01 Добавил папку промежуточного отчета
    [CarbonTubeD16mmL0.5m.SLDPRT, CarbonTubeD16mmL1m.SLDPRT, CarbonTubeD16mmL2m.SLDPRT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]
2024-05-01 Добавил смету на полетный контроллер (требует уточнения)
    [Costings.xlsx]
2024-05-01 Добавлен файл фюзеляжа
    [18650 Li-Ion.step, BatteryHolder.SLDPRT, CarbonTubeD16mmL0.5m.SLDPRT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]
2024-05-03 Small refinments
    [WingLeft.SLDASM, WingRight.SLDASM, XPSWingPart500mm.SLDPRT]
2024-05-03 Add files via upload
    добавление силового набора с обтянутых поверхностей
    [ГО.SLDPRT, балка 1м х 20мм 1мм стенка.SLDPRT, киль naca0006.SLDPRT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]
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2024-05-03 Add files via upload
    киль
    [Fin.SLDPRT]
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2024-05-03 Добавил файл прототипа фюзеляжа
    [CarbonTubeD20mmL1.2m.SLDPRT, Fin.SLDPRT, MotorMount.SLDASM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]
2024-05-04 Добавлена папка Assembly2(current)
    [CarbonTubeD20mmL1.2m.SLDPRT, Fin.SLDPRT, WingAssemble.SLDASM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]
2024-05-04 Add image
    [ГО.SLDPRT, крыло naca4412.SLDPRT]
2024-05-05 Отрисовал фюзеляж в папке Assembly3
    [AileronEnclosureXPS.SLDPRT, Ailerons(Flaps).SLDASM, CarbonTubeD10mmL1m.SLDPRT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]
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2024-05-06 Перенес старую версию графика работ
    [GanttChart.xlsx]
2024-05-06 Таблица с авионикой
    [Avionics.xlsx]
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2024-05-06 Добавил описание БО
    [AP-PR-006_6-2_RH.stp, CarbonTubeD20mmL1.2m.SLDPRT, Fuselage3.SLDPRT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]
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2024-05-06 Дописал описание датчиков
    [Avionics.xlsx, Fuselage3.SLDPRT]
2024-05-06 Добавил актуальную версию промежуточного отчета
    [Avionics.xlsx, Sensors.xlsx, airfoil.xlsx]
2024-05-07 Add files via upload
    дописана моя часть отчета, это прямой потомок template (1)
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2024-05-08 Переупорядочил папки
    [Cd.csv, Cl.csv, Fuselage3.SLDPRT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]
2024-05-18 Добавил смету на самолет
    [CostingsFlightController.xlsx, CostingsMaterial.xlsx]
2024-05-18 Добавил новые позиции в смете
    [CostingsMaterial.xlsx]
2024-05-18 Новые позиции в смете
    [CostingsMaterial.xlsx]
2024-05-19 Добавил папку производственного отчета
    [global_parameters.txt, study.SLDPRT]
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2024-05-19 Добавлена папка с детальным отчетом
    [GanttChartDetailedReport.xlsx]
2024-05-19 Добавлена папка детальной модели
    [11x7 UL SS.SLDPRT, Assembly.SLDASM, Propeller.SLDPRT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]
2024-05-19 Добавлено исследование аэродинамики в SW
    [global_parameters.txt, study.SLDPRT]
2024-05-20 Добавил обновленный график работ
    [Assembly.SLDASM, GanttChartDetailedReport.xlsx]
2024-05-21 Add some images
    [Assembly.SLDASM, global_parameters.txt, study.SLDPRT]
2024-05-26 New study
    [11x7 UL SS.SLDPRT, Assembly.SLDASM, Fuselage3.SLDPRT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]
2024-05-26 add study
    [global_parameters.txt]
2024-06-10 Добавил детализированную модель
    [1.9mWingspan.xlsx, 1.9mWingspanFuselageMesh.xlsx, 3AA.xlsx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]
2024-06-10 Добавил стенд для ПК
    [standPart1.SLDPRT, standPart2.SLDPRT, standPart3.SLDPRT]
2024-06-10 Modified rib and cargo
    [Rib250mmSketch.SLDPRT, cargo.SLDPRT]
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2024-06-12 Добавил STL файл для фюзеляжа
    [CrossSection1.SLDPRT, CrossSection2.SLDPRT, FusNose4mm.SLDPRT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]
2024-07-06 Создал папку производственного отчета
    [1.9mWingspan.xlsx, 1.9mWingspanFuselageMesh.xlsx, 3AA.xlsx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]
2024-07-06 убрал лишние папки
    [GanttChartDetailedReport.xlsx]
2024-07-06 Deleted unused folders
    [1.9mWingspan.xlsx, 1.9mWingspanFuselageMesh.xlsx, 3AA.xlsx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]
2024-07-08 add dxf files
    [Aileron170mmNACA0010.DXF, AileronRib170mmNACA0010.DWG, AileronRib170mmNACA0010.DXF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]
2024-07-20 Add new airfoil SD7032
    [NACA0009_100poits_rotation.xlsx, SD7032_100points_rotation.xlsx]
2024-07-20 Add new simulation with SD7032
    [0AOA.xlsx, ELEVATOR.SLDPRT, FuselageSG7032.SLDPRT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]
2024-07-20 Add new files for laser cutting
    [Ailerons.DXF, AileronsServo.DXF, ConnectorLongPart2.DXF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]
2024-07-20 Add new light weight wing
    [16_7.4mmRibConnector.SLDPRT, 16_7.4mmTubeConnector.SLDPRT, 16_7mmConnector.SLDPRT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]
2024-07-20 Add new files for 3d printing
    [16_7.4mmRibConnector.STL, 16_7.4mmTubeConnector.STL, 16_8.4mmConnector.3mf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]
2024-07-20 Model has been updated
    [1.9mWingspan.xlsx, 1.9mWingspanFuselageMesh.xlsx, 3AA.xlsx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]
2024-07-20 Add manufacturing design
    [Deflection.xlsx, coef.xlsx]
2024-07-20 Update costings
    [Costings.xlsx, CostingsFlightController.xlsx, CostingsMaterial.xlsx]
2024-07-20 Reorganize folders
    [0AOA.xlsx, 16_7.4mmRibConnector.SLDPRT, 16_7.4mmRibConnector.STL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]
2024-07-20 Rename Manufacturing folder
    [0AOA.xlsx, 16_7.4mmRibConnector.SLDPRT, 16_7.4mmRibConnector.STL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]
2024-09-23 Add fully 3D Printed Assembly
    [Aileron.SLDPRT, AileronInfill.STL, AileronInfillLeft.STL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]
